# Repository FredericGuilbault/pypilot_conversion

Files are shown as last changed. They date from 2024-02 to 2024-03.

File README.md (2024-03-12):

# pypilot_conversion
Details of converting a ST1000/ST2000 tiller pilot into a PyPilot implementation.

## Converting your own. 

#### getting the boards 
most if not any PCB(Printed circuit board) manifacturer works with gerber files, the pypilot_conversion is made of 3 PBC:
 - pypilot_motor
 - pypilot_keyboard
 - pypilot_dome

#### getting the parts
Each board also have a part list of electronics components you will need to solder on the boards. Commonly named BOM(bills of material)

####  Building
Build notes:

- Had to flip one resistor on the keyboard to the front; otherwise it was in the way of a piece of the plastic casing. Also had to tilt the buckdown converter to its side.

- The current measuring is still a bit in progress. The Pololu CS (current sense) pin is supposed to give 'about 20 mV/A plus a 50 mV offset', but setting the servo.current.factor and .offset was not enough; I tweaked motor.ino a bit but don't get a linear reading so far.

Images from the building process: https://photos.app.goo.gl/vQ7VHdccvfHCTUkM7

####  Software
To be used in combination with pypilot_ray replacing pypilot_hat.

https://github.com/marcobergman/pypilot_ray

## Developpement

Work in progress; details follow in due time. Based on a prototype described here https://forum.openmarine.net/showthread.php?tid=1864&pid=9664#pid9664



First findings impression: https://www.youtube.com/watch?v=vbth_teGMJA



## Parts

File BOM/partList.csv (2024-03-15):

Source: | pypilot_conversion/kicadFiles/pypilot.kicad_sch
Date: | Fri 15 Mar 2024 04:44:39 AM
Tool: | Eeschema 6.0.11+dfsg-1
Generator: | /usr/share/kicad/plugins/bom_csv_grouped_by_value.py
Component Count: | 51
Individual Components:
Item | Qty | Reference(s) | Value | LibPart | Footprint | Datasheet
 |  | A1 | MH-MINI-360 | pypilot:MH-MINI-360 | pypilot:MH-MINI-360 | Mini-360 DC-DC Buck Converter
 |  | A2 | MPU-9255 | pypilot:MPU-9255 | Connector_PinHeader_2.54mm:PinHeader_1x04_P2.54mm_Vertical | MPU9255 3-axis gyroscope, 3-axis accelerometer, and 3-axis compass/magnetometer
 |  | A3 | Arduino_Nano | MCU_Module:Arduino_Nano_Every | Module:Arduino_Nano | https://content.arduino.cc/assets/NANOEveryV3.0_sch.pdf
 |  | A4 | Pololu#2991 | pypilot:Pololu#2992 | pypilot:Pololu#2991 | Pololu G2 High Power Motor Driver 17A, 6.5V-30V
 |  | BZ1 | Buzzer | Device:Buzzer | Buzzer_Beeper:Buzzer_TDK_PS1240P02BT_D12.2mm_H6.5mm | https://cdn.robotshop.com/media/s/spa/rb-spa-1091/pdf/cem-1203-42-.pdf
 |  | C1 | 0.1uF | Device:C_Small | Capacitor_THT:C_Disc_D6.0mm_W2.5mm_P5.00mm | 100nf or 0.1uf #104
 |  | C2 | 10uF | pypilot-rescue:CP_Small-Device | Capacitor_THT:CP_Radial_D10.0mm_P5.00mm
 |  | C3 | 10uF | pypilot-rescue:CP_Small-Device | Capacitor_THT:CP_Radial_D10.0mm_P5.00mm
 |  | C4 | 0.1uF | Device:C_Small | Capacitor_THT:C_Disc_D6.0mm_W2.5mm_P5.00mm | 100nf or 0.1uf #104
 |  | C5 | 0.1uF | Device:C_Small | Capacitor_THT:C_Disc_D6.0mm_W2.5mm_P5.00mm | 100nf or 0.1uf #104
 |  | C6 | 10uF | pypilot-rescue:CP_Small-Device | Capacitor_THT:CP_Radial_D10.0mm_P5.00mm
 |  | C7 | 0.1uF | Device:C_Small | Capacitor_THT:C_Disc_D6.0mm_W2.5mm_P5.00mm | 100nf or 0.1uf #104
 |  | C8 | 10uF | pypilot-rescue:CP_Small-Device | Capacitor_THT:CP_Radial_D10.0mm_P5.00mm
 |  | C9 | 470uF | pypilot-rescue:CP_Small-Device | Capacitor_THT:CP_Radial_D10.0mm_P5.00mm
 |  | D1 | LED | Device:LED | LED_THT:LED_D3.0mm | ~
 |  | D2 | green | Device:LED | LED_THT:LED_D3.0mm | ~
 |  | D3 | red | Device:LED | LED_THT:LED_D3.0mm | ~
 |  | H1 | MountingHole | Mechanical:MountingHole | MountingHole:MountingHole_2.7mm | ~
 |  | J1 | Power +12V | Connector_Generic:Conn_01x01 | pypilot:tab | ~
 |  | J2 | Power 0V | Connector_Generic:Conn_01x01 | pypilot:tab | ~
 |  | J3 | 2x6 | Connector_Generic:Conn_02x06_Odd_Even | Connector_PinHeader_2.54mm:PinHeader_2x06_P2.54mm_Vertical | ~
 |  | J4 | 12V | Connector_Generic:Conn_01x01 | pypilot:tab | ~
 |  | J5 | 12V | Connector_Generic:Conn_01x01 | pypilot:tab | ~
 |  | J6 | 1x4 | Connector_Generic:Conn_01x04 | Connector_PinHeader_2.54mm:PinHeader_1x04_P2.54mm_Vertical | ~
 |  | J7 | 1x4 | Connector_Generic:Conn_01x04 | Connector_PinHeader_2.54mm:PinHeader_1x04_P2.54mm_Vertical | ~
 |  | J8 | Motor A | Connector_Generic:Conn_01x01 | pypilot:tab | ~
 |  | J9 | End Stops | Connector_Generic:Conn_01x04 | Connector_PinHeader_2.54mm:PinHeader_1x04_P2.54mm_Vertical | ~
 |  | J10 | PiZero W | Connector:Raspberry_Pi_2_3 | Connector_PinSocket_2.54mm:PinSocket_2x20_P2.54mm_Vertical | https://www.raspberrypi.org/documentation/hardware/raspberrypi/schematics/rpi_SCH_3bplus_1p0_reduced.pdf
 |  | J11 | Motor B | Connector_Generic:Conn_01x01 | pypilot:tab | ~
 |  | J12 | GND | Connector_Generic:Conn_01x01 | pypilot:tab | ~
 |  | J13 | GND | Connector_Generic:Conn_01x01 | pypilot:tab | ~
 |  | Q1 | BC547 | Transistor_BJT:BC547 | Package_TO_SOT_THT:TO-92 | https://www.onsemi.com/pub/Collateral/BC550-D.pdf
 |  | R1 | 1k2 | Device:R | Resistor_THT:R_Axial_DIN0309_L9.0mm_D3.2mm_P12.70mm_Horizontal | ~
 |  | R2 | 1k | Device:R | Resistor_THT:R_Axial_DIN0309_L9.0mm_D3.2mm_P12.70mm_Horizontal | ~
 |  | R3 | 10k | Device:R | Resistor_THT:R_Axial_DIN0309_L9.0mm_D3.2mm_P12.70mm_Horizontal | ~
 |  | R4 | 10k | Device:R | Resistor_THT:R_Axial_DIN0309_L9.0mm_D3.2mm_P12.70mm_Horizontal | ~
 |  | R5 | 100 | Device:R | Resistor_THT:R_Axial_DIN0309_L9.0mm_D3.2mm_P12.70mm_Horizontal | ~
 |  | R6 | 560 | Device:R | Resistor_THT:R_Axial_DIN0309_L9.0mm_D3.2mm_P12.70mm_Horizontal | ~
 |  | R7 | 10k | Device:R | Resistor_THT:R_Axial_DIN0309_L9.0mm_D3.2mm_P12.70mm_Horizontal | ~
 |  | R8 | 2k2 | Device:R | Resistor_THT:R_Axial_DIN0309_L9.0mm_D3.2mm_P12.70mm_Horizontal | ~
 |  | R9 | 560 | Device:R | Resistor_THT:R_Axial_DIN0309_L9.0mm_D3.2mm_P12.70mm_Horizontal | ~
 |  | R10 | 560 | Device:R | Resistor_THT:R_Axial_DIN0309_L9.0mm_D3.2mm_P12.70mm_Horizontal | ~
 |  | SW1 | Auto | Switch:SW_Push | pypilot:SW_PUSH_6mm | ~
 |  | SW2 | StdBy | Switch:SW_Push | pypilot:SW_PUSH_6mm | ~
 |  | SW3 | -10 | Switch:SW_Push | pypilot:SW_PUSH_6mm | ~
 |  | SW4 | -1 | Switch:SW_Push | pypilot:SW_PUSH_6mm | ~
 |  | SW5 | 1 | Switch:SW_Push | pypilot:SW_PUSH_6mm | ~
 |  | SW6 | 10 | Switch:SW_Push | pypilot:SW_PUSH_6mm | ~
 |  | SW7 | SB | Switch:SW_Push | pypilot:SW_PUSH_6mm | ~
 |  | SW8 | BB | Switch:SW_Push | pypilot:SW_PUSH_6mm | ~
 |  | TH1 | Handle | Device:Thermistor | Resistor_THT:R_Axial_DIN0309_L9.0mm_D3.2mm_P5.08mm_Vertical | This is just an handle to fix the cover on.
Collated Components:
Item | Qty | Reference(s) | Value | LibPart | Footprint | Datasheet
1 | 1 | A1 | MH-MINI-360 | pypilot:MH-MINI-360 | pypilot:MH-MINI-360 | Mini-360 DC-DC Buck Converter
2 | 1 | A2 | MPU-9255 | pypilot:MPU-9255 | Connector_PinHeader_2.54mm:PinHeader_1x04_P2.54mm_Vertical | MPU9255 3-axis gyroscope, 3-axis accelerometer, and 3-axis compass/magnetometer
3 | 1 | A3 | Arduino_Nano | MCU_Module:Arduino_Nano_Every | Module:Arduino_Nano | https://content.arduino.cc/assets/NANOEveryV3.0_sch.pdf
4 | 1 | A4 | Pololu#2991 | pypilot:Pololu#2992 | pypilot:Pololu#2991 | Pololu G2 High Power Motor Driver 17A, 6.5V-30V
5 | 1 | BZ1 | Buzzer | Device:Buzzer | Buzzer_Beeper:Buzzer_TDK_PS1240P02BT_D12.2mm_H6.5mm | https://cdn.robotshop.com/media/s/spa/rb-spa-1091/pdf/cem-1203-42-.pdf
6 | 4 | C1, C4, C5, C7 | 0.1uF | Device:C_Small | Capacitor_THT:C_Disc_D6.0mm_W2.5mm_P5.00mm | 100nf or 0.1uf #104
7 | 4 | C2, C3, C6, C8 | 10uF | pypilot-rescue:CP_Small-Device | Capacitor_THT:CP_Radial_D10.0mm_P5.00mm
8 | 1 | C9 | 470uF | pypilot-rescue:CP_Small-Device | Capacitor_THT:CP_Radial_D10.0mm_P5.00mm
9 | 1 | D1 | LED | Device:LED | LED_THT:LED_D3.0mm | ~
10 | 1 | D2 | green | Device:LED | LED_THT:LED_D3.0mm | ~
11 | 1 | D3 | red | Device:LED | LED_THT:LED_D3.0mm | ~
12 | 1 | H1 | MountingHole | Mechanical:MountingHole | MountingHole:MountingHole_2.7mm | ~
13 | 1 | J1 | Power +12V | Connector_Generic:Conn_01x01 | pypilot:tab | ~
14 | 1 | J2 | Power 0V | Connector_Generic:Conn_01x01 | pypilot:tab | ~
15 | 1 | J3 | 2x6 | Connector_Generic:Conn_02x06_Odd_Even | Connector_PinHeader_2.54mm:PinHeader_2x06_P2.54mm_Vertical | ~
16 | 2 | J4, J5 | 12V | Connector_Generic:Conn_01x01 | pypilot:tab | ~
17 | 2 | J6, J7 | 1x4 | Connector_Generic:Conn_01x04 | Connector_PinHeader_2.54mm:PinHeader_1x04_P2.54mm_Vertical | ~
18 | 1 | J8 | Motor A | Connector_Generic:Conn_01x01 | pypilot:tab | ~
19 | 1 | J9 | End Stops | Connector_Generic:Conn_01x04 | Connector_PinHeader_2.54mm:PinHeader_1x04_P2.54mm_Vertical | ~
20 | 1 | J10 | PiZero W | Connector:Raspberry_Pi_2_3 | Connector_PinSocket_2.54mm:PinSocket_2x20_P2.54mm_Vertical | https://www.raspberrypi.org/documentation/hardware/raspberrypi/schematics/rpi_SCH_3bplus_1p0_reduced.pdf
21 | 1 | J11 | Motor B | Connector_Generic:Conn_01x01 | pypilot:tab | ~
22 | 2 | J12, J13 | GND | Connector_Generic:Conn_01x01 | pypilot:tab | ~
23 | 1 | Q1 | BC547 | Transistor_BJT:BC547 | Package_TO_SOT_THT:TO-92 | https://www.onsemi.com/pub/Collateral/BC550-D.pdf
24 | 1 | R1 | 1k2 | Device:R | Resistor_THT:R_Axial_DIN0309_L9.0mm_D3.2mm_P12.70mm_Horizontal | ~
25 | 1 | R2 | 1k | Device:R | Resistor_THT:R_Axial_DIN0309_L9.0mm_D3.2mm_P12.70mm_Horizontal | ~
26 | 3 | R3, R4, R7 | 10k | Device:R | Resistor_THT:R_Axial_DIN0309_L9.0mm_D3.2mm_P12.70mm_Horizontal | ~
27 | 1 | R5 | 100 | Device:R | Resistor_THT:R_Axial_DIN0309_L9.0mm_D3.2mm_P12.70mm_Horizontal | ~
28 | 3 | R6, R9, R10 | 560 | Device:R | Resistor_THT:R_Axial_DIN0309_L9.0mm_D3.2mm_P12.70mm_Horizontal | ~
29 | 1 | R8 | 2k2 | Device:R | Resistor_THT:R_Axial_DIN0309_L9.0mm_D3.2mm_P12.70mm_Horizontal | ~
30 | 1 | SW1 | Auto | Switch:SW_Push | pypilot:SW_PUSH_6mm | ~
31 | 1 | SW2 | StdBy | Switch:SW_Push | pypilot:SW_PUSH_6mm | ~
32 | 1 | SW3 | -10 | Switch:SW_Push | pypilot:SW_PUSH_6mm | ~
33 | 1 | SW4 | -1 | Switch:SW_Push | pypilot:SW_PUSH_6mm | ~
34 | 1 | SW5 | 1 | Switch:SW_Push | pypilot:SW_PUSH_6mm | ~
35 | 1 | SW6 | 10 | Switch:SW_Push | pypilot:SW_PUSH_6mm | ~
36 | 1 | SW7 | SB | Switch:SW_Push | pypilot:SW_PUSH_6mm | ~
37 | 1 | SW8 | BB | Switch:SW_Push | pypilot:SW_PUSH_6mm | ~
38 | 1 | TH1 | Handle | Device:Thermistor | Resistor_THT:R_Axial_DIN0309_L9.0mm_D3.2mm_P5.08mm_Vertical | This is just an handle to fix the cover on.

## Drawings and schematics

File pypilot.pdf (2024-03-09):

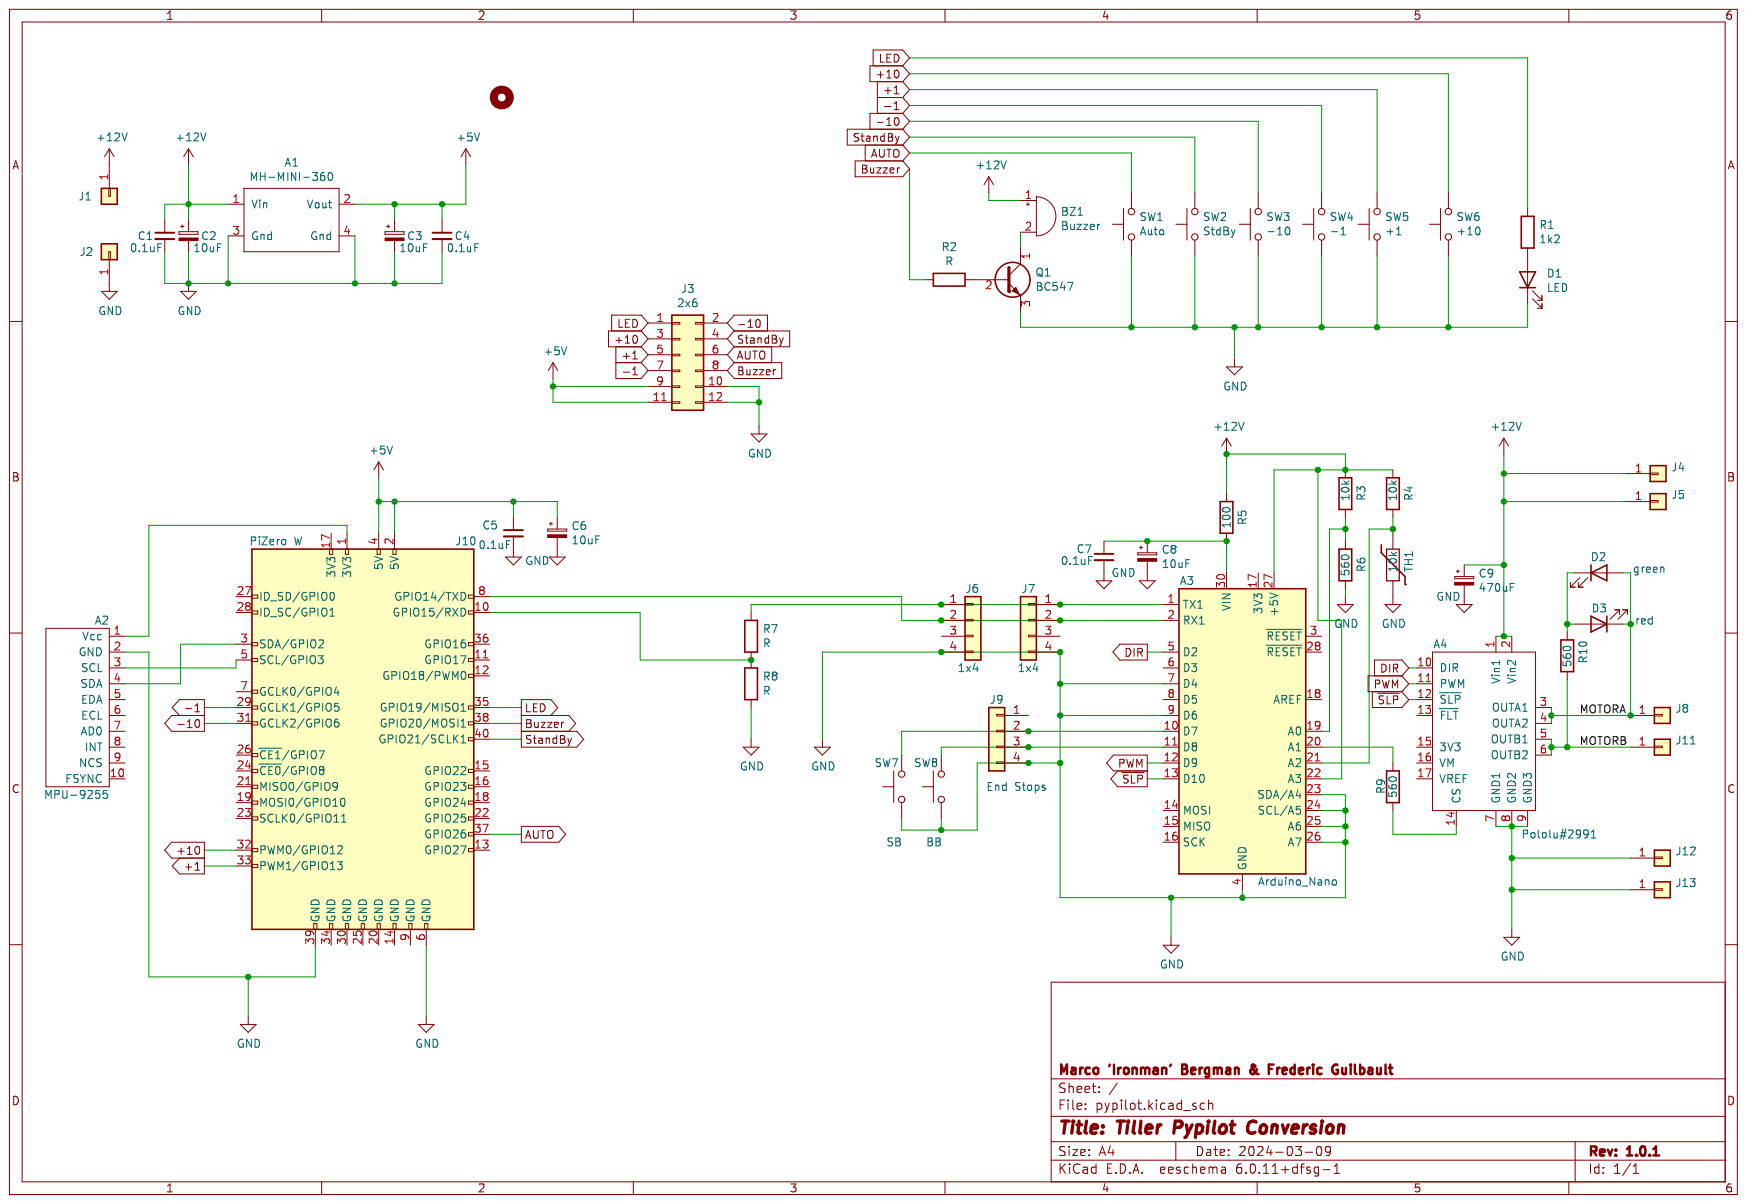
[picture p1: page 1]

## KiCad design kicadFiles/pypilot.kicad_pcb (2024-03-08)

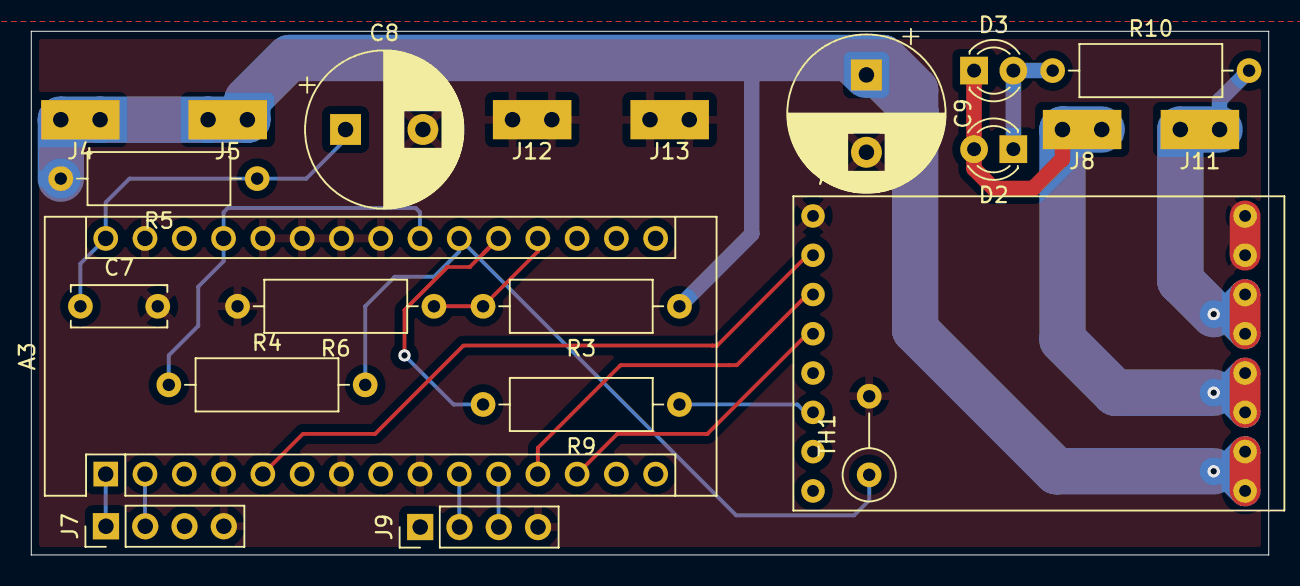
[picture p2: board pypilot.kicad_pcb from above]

Board: 2 copper layers, 80.0 x 33.9 mm, 22 parts (0 on the bottom side), 18 nets.

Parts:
A3: Arduino_Nano
A4: pololu#2991; Pololu#2991
C7: 0.1uF; C_Disc_D6.0mm_W2.5mm_P5.00mm
C8: 10uF; CP_Radial_D10.0mm_P5.00mm
C9: 470uF; CP_Radial_D10.0mm_P5.00mm
D2: green; LED_D3.0mm
D3: red; LED_D3.0mm
J4, J5: 12V; tab
J7: 1x4; PinHeader_1x04_P2.54mm_Vertical
J8: Motor A; tab
J9: End Stops; PinHeader_1x04_P2.54mm_Vertical
J11: Motor B; tab
J12, J13: GND; tab
R3, R4: 10k; R_Axial_DIN0309_L9.0mm_D3.2mm_P12.70mm_Horizontal
R5: 100; R_Axial_DIN0309_L9.0mm_D3.2mm_P12.70mm_Horizontal
R6, R9, R10: 560; R_Axial_DIN0309_L9.0mm_D3.2mm_P12.70mm_Horizontal
TH1: 10k; R_Axial_DIN0309_L9.0mm_D3.2mm_P5.08mm_Vertical

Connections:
+12V: A4.1, A4.2, C9.1, J4.1, J5.1, R3.1, R5.2
/MOTORA: A4.3, A4.4, D2.2, D3.1, J8.1
/MOTORB: A4.5, A4.6, J11.1, R10.2
DIR: A3.5, A4.10
GND: A3.4, A3.7, A3.9, A3.23, A3.24, A3.25, A3.26, A3.29, A4.7, A4.8, A4.9, C7.2, C8.2, C9.2, J7.4, J9.4, J12.1, J13.1, R6.2, TH1.2
unnamed: A3.1, J7.1
unnamed: A3.2, J7.2
unnamed: A3.10, J9.2
unnamed: A3.11, J9.3
unnamed: A3.19, R3.2, R6.1
unnamed: A3.20, R9.2
unnamed: A3.21, R4.2, TH1.1
unnamed: A3.22, A3.27, R4.1
unnamed: A3.30, C7.1, C8.1, R5.1
unnamed: A4.14, R9.1
unnamed: D2.1, D3.2, R10.1
PWM: A3.12, A4.11
~SLP: A3.13, A4.12

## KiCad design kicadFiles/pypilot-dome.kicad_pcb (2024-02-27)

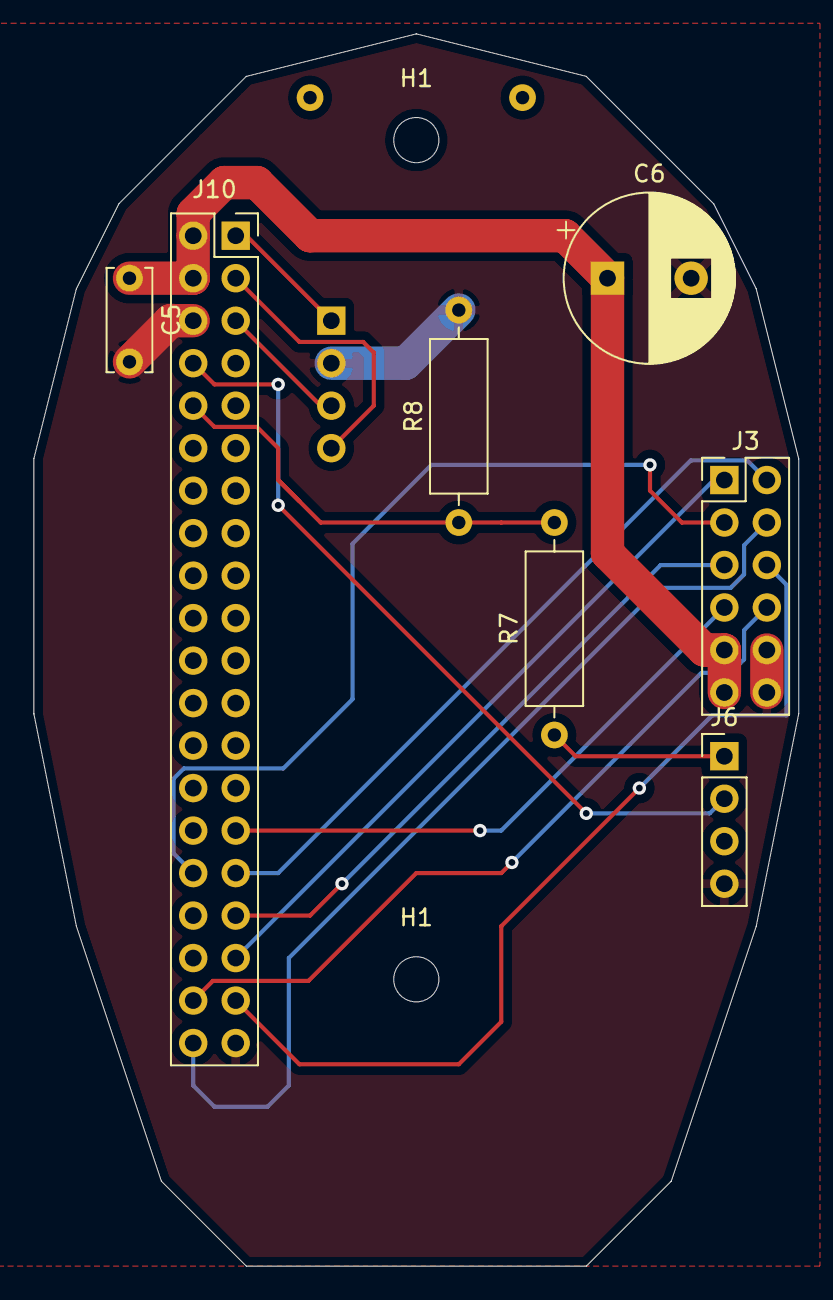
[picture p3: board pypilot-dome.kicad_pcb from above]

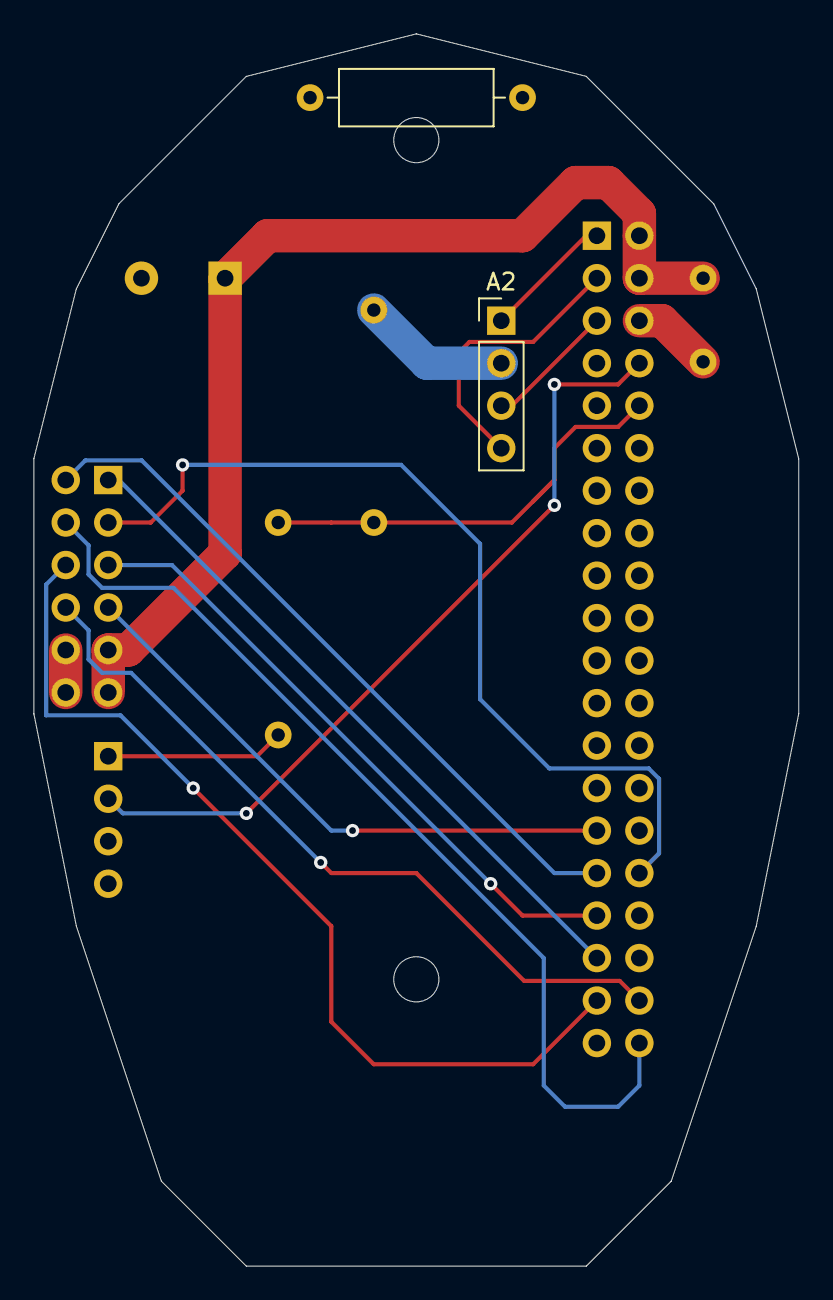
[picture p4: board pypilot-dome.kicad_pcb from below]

Board: 2 copper layers, 45.7 x 73.7 mm, 11 parts (2 on the bottom side), 16 nets.

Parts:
A2: MPU-9255; PinHeader_1x04_P2.54mm_Vertical
C5: 0.1uF; C_Disc_D6.0mm_W2.5mm_P5.00mm
C6: 10uF; CP_Radial_D10.0mm_P5.00mm
H1, H1#2: MountingHole; MountingHole_2.7mm
J3: 2x6; PinHeader_2x06_P2.54mm_Vertical
J6: 1x4; PinHeader_1x04_P2.54mm_Vertical
J10: PiZero W; PinSocket_2x20_P2.54mm_Vertical
R7, R8: R; R_Axial_DIN0309_L9.0mm_D3.2mm_P12.70mm_Horizontal
R10: 560; R_Axial_DIN0309_L9.0mm_D3.2mm_P12.70mm_Horizontal

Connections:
+1: J3.5, J10.33
+5V: C5.1, C6.1, J3.9, J3.11, J10.2, J10.4
+10: J3.3, J10.32
-1: J3.7, J10.29
-10: J3.2, J10.31
AUTO: J3.6, J10.37
Buzzer: J3.8, J10.38
GND: A2.2, C5.2, C6.2, J3.10, J3.12, J6.4, J10.6, J10.39, R8.2
LED: J3.1, J10.35
unnamed: A2.1, J10.1
unnamed: A2.3, J10.5
unnamed: A2.4, J10.3
unnamed: J6.1, R7.1
unnamed: J6.2, J10.8
unnamed: J10.10, R7.2, R8.1
StandBy: J3.4, J10.40

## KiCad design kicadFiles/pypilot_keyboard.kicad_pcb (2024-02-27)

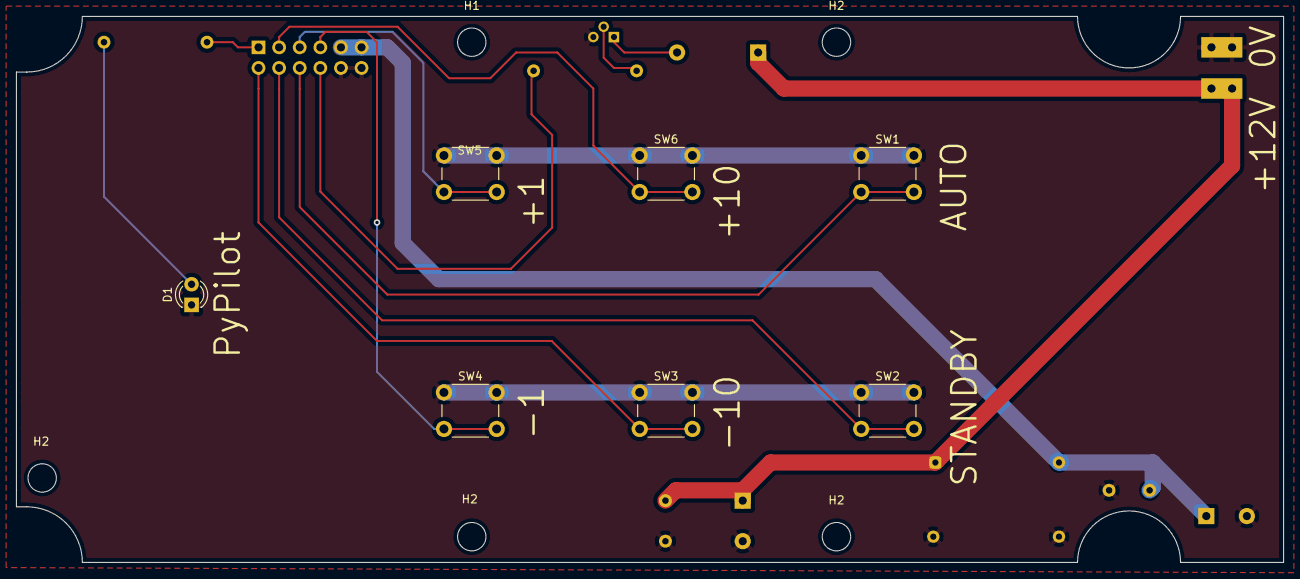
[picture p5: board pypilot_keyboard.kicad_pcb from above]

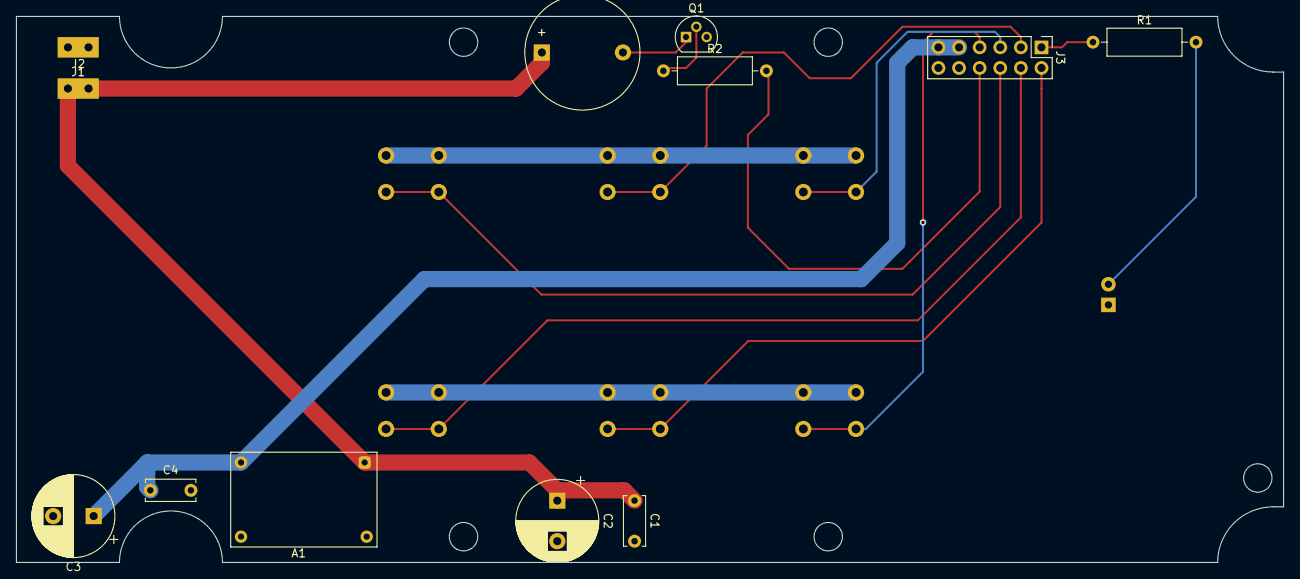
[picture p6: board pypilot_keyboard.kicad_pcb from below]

Board: 2 copper layers, 156.2 x 67.3 mm, 24 parts (12 on the bottom side), 14 nets.

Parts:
A1: MH-MINI-360
BZ1: Buzzer; Buzzer_D14mm_H7mm_P10mm
C1, C4: 0.1uF; C_Disc_D6.0mm_W2.5mm_P5.00mm
C2, C3: 10uF; CP_Radial_D10.0mm_P5.00mm
D1: LED; LED_D3.0mm
H1, H2, H2#2, H2#3, H2#4: MountingHole; MountingHole_3.5mm
J1: Power +12V; tab
J2: Power 0V; tab
J3: 2x6; PinHeader_2x06_P2.54mm_Vertical
Q1: BC547; TO-92
R1: 1k2; R_Axial_DIN0309_L9.0mm_D3.2mm_P12.70mm_Horizontal
R2: R; R_Axial_DIN0309_L9.0mm_D3.2mm_P12.70mm_Horizontal
SW1: Auto; SW_PUSH_6mm
SW2: StdBy; SW_PUSH_6mm
SW3: -10; SW_PUSH_6mm
SW4: -1; SW_PUSH_6mm
SW5: +1; SW_PUSH_6mm
SW6: +10; SW_PUSH_6mm

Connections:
+1: J3.5, SW5.2
+5V: A1.2, C3.1, C4.1, J3.9, J3.11
+10: J3.3, SW6.2
+12V: A1.1, BZ1.1, C1.1, C2.1, J1.1
-1: J3.7, SW4.2
-10: J3.2, SW3.2
AUTO: J3.6, SW1.2
Buzzer: J3.8, R2.2
GND: A1.3, A1.4, C1.2, C2.2, C3.2, C4.2, D1.1, J2.1, J3.10, J3.12, Q1.3, SW1.1, SW2.1, SW3.1, SW4.1, SW5.1, SW6.1
LED: J3.1, R1.1
unnamed: BZ1.2, Q1.1
unnamed: D1.2, R1.2
unnamed: Q1.2, R2.1
StandBy: J3.4, SW2.2

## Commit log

2024-02-27 remove zipped content, restructure files location.
    [partlist_pypilot-dome.csv, partlist_pypilot-motor.csv, partlist_pypilot_keyboard.csv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]
2024-03-08 Fix Problem where motor wrongly report 170°C due to error in wiring
    [pypilot-B_Cu.gbl, pypilot-B_Mask.gbs, pypilot-B_Paste.gbp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]
2024-03-09 2nd Fix Problem where motor wrongly report 170°C due to error in wiring
    [pypilot-motor.kicad_pcb, pypilot.kicad_sch]
2024-03-12 Update gerber files
    [pypilot-B_Cu.gbl, pypilot-B_Mask.gbs, pypilot-B_Paste.gbp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]
2024-03-15 add details to the BOM
    [partList.csv, partlist_pypilot-dome.csv, partlist_pypilot-motor.csv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]
